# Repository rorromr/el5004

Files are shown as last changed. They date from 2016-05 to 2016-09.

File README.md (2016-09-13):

# EL5004: Teleoperación de Go Kart



Desarrollo de un sistema de actuación y teleoperación de un vehículo tipo Go Kart.

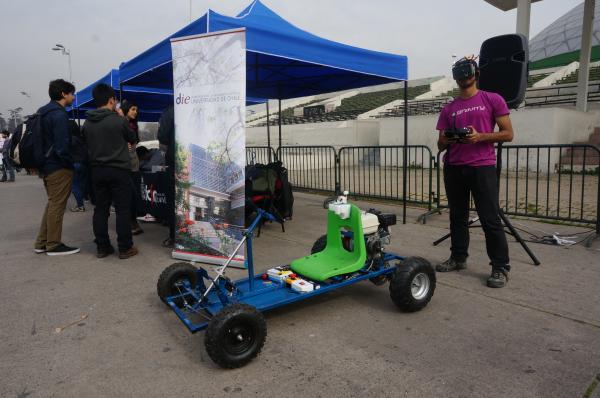
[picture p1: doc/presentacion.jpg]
 

Estructura:

```
el5004
|
+-- arduino [Software]
|
+-- doc [Documentación]
|
+-- cad [Archivos CAD]
|
+-- gokart_serial [Interfaz serial con PC]
|
+-- pcb [Diseño PCB]
|
+-- scripts [Scripts de compilación y CI]
```

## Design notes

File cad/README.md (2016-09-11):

# EL5004: Teleoperación de Go Kart

## CAD

Los archivos CAD fueron creados usando SolidWorks 2014 y estan disponibles [aquí](https://mega.nz/#!sts3RLpC!TGG8FULg5RGBNG4SyLwB-OSzpaIaMvL-rCDUFSoWiwc).

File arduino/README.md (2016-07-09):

# EL5004: Teleoperación de Go Kart

## Código para Arduino

La plataforma de desarrollo corresponde a Arduino Mega 2560.

El software se ha estructurado como una librería de Arduino. Para más información ver [librerías de Arduino]( https://www.arduino.cc/en/Guide/Libraries).

El directorio para la instalación de librerías de Arduino suele ser:
* Linux: `~/Arduino/libraries`
* OS X: `Documents/Arduino/libraries`
* Windows: `My Documents\Arduino\libraries`

## Librerías

### Dynamixel

Esta librería emplea la conexión serial 1 de Arduino Mega (TX1, RX1). El pin usado para cambiar la dirección de comunicación es configurado en el método `begin` de la librería. 

#### Instalación

Copiar el directorio `DynamixelSerial1` en `~/Arduino/libraries`

### GoKart

Contiene el código para el control del vehiculo GoKart.

```
arduino
|
+-- GoKart [Librería principal]
|   |
|   +-- examples
|       |-- dynamixel_test [Test de motores Dynamixel]
|       |-- gokart_dynamixel [Test motores Dynamixel usando interfaz GoKart]
|       |-- gokart_integration [Desarrollo de software principal]
|       |-- gokart_lcd_test [Test de pantalla LCD]
|       |-- msg_test [Test de serialización de mensajes]
|       |-- rf_test [Test de comunicación RF]
|       |-- rf_test2 [Test de comunicación RF con salida serial más rápida]
|       |-- serial_test [Test de comunicación serial]
|
```
#### Instalación

Copiar el directorio `GoKart` en `~/Arduino/libraries`

#### Problemas conocidos

La librería para el control de motores Dynamixel solo funciona usando un baudrate de 1.000.000 baud/s.

## Datasheet EX106

[Documento PDF](http://www.hizook.com/files/users/3/EX-106_Robotis_Dynamixel_Servo_UserGuide.pdf)

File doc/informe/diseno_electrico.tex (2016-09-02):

\section{Diseño eléctrico}

En esta sección se muestran los distintos elementos del desarrollo en el plano eléctrico y electrónico.

\subsection{Diagrama eléctrico}

La Figura \ref{de_diagrama} muestra el diagrama eléctrico principal, este cuenta con los siguientes elementos:
\begin{itemize}
    \item \textbf{Batería}: La batería corresponde a un pack de 4 celdas de polímero de litio. Posee un voltaje nominal de \SI{14.8}{\volt} y una capacidad de \SI{3300}{\milli\ampere\hour}. Este tipo de baterías se caracterizan por su gran densidad energética y capacidad de descarga, por lo es óptima para la operación de motores, pues usualmente requieren peaks corriente del orden de \SI{5}{\ampere}.
    \item \textbf{Panel de control}: En su interior contiene el microcontrolador y receptor de radio.
    \item \textbf{Interruptor principal}: Es el encargado de conectar la batería con el resto de los circuitos.
    \item \textbf{Interruptor de emergencia}: Desconecta la energía del bus de actuadores Dynamixel, no interfiere con la alimentación del panel de control.
    \item \textbf{Bus Dynamixel}: Este bus esta constituido por cuatro conductores. Dos de ellos proporcionan alimentación a los dispositivos conectados ($V_{cc}$ y tierra). Los otros dos corresponden a la señal diferencial del bus RS485.
\end{itemize}

\begin{figure}[H]
\begin{center}
	
	\caption{Diagrama elétrico principal.}
	\label{de_diagrama}
\end{center}
\end{figure}

\subsection{Sistema de radio}

Para la comunicación con el GoKart a través de telecomandos se está utilizando un transmisor de radiofrecuencias llamado Fly-Sky modelo FS-T6, junto a un receptor de 6 canales a 2.4 GHz llamado Fly-Sky modelo FS-R6B (ver en Figura \ref{rf}).

\begin{figure}[H]
    \centering
    \begin{subfigure}[b]{0.3\textwidth}
        \centering
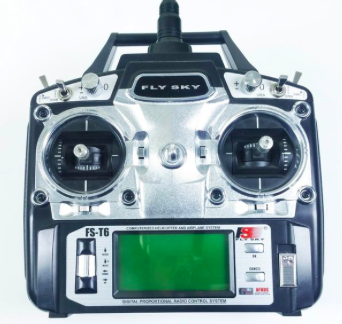
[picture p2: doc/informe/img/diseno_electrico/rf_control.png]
        
        \caption{Control remoto}
        \label{rf_control}
    \end{subfigure}
    \begin{subfigure}[b]{0.3\textwidth}
        \centering
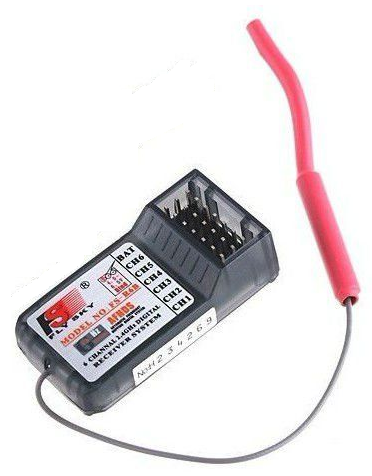
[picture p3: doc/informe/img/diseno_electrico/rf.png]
        
	    \caption{Receptor de radio}
	    \label{rf_img}
    \end{subfigure}
    \caption{Hardware utilizado para telecomandar el gokart}\label{rf}
\end{figure}

De la radio transmisora se utilizarán 3 comandos:
\begin{enumerate}
    \item {\textbf{Manilla izquierda:} movimientos UP y DOWN para acelerar y frenar, respectivamente.}
    \item {\textbf{Manilla derecha: } movimientos LEFT y RIGHT para dirección.}
    \item {\textbf{Switch superior izquierda:} para activar estado de emergencia. }
\end{enumerate}

De esta forma, el receptor utiliza 3 de sus 6 canales para recibir los datos, los que resultan ser números enteros con un rango entre 1000-1400, que corresponden al valor en \si{\micro\second} del up-time de la señal PWM recibida.

\subsection{Sistema embebido}

El sistema cuenta con un microcontrolador principal encargado de recibir los comandos desde el receptor de radio y enviar comandos de movimiento a los servomotores. El sistema usa como elemento principal una placa de desarrollo Arduino Mega 2560 \cite{arduino_mega}, que se muestra en la Figura \ref{arduino_mega_img}. La Tabla \ref{arduino_mega_tab} muestra las principales características de la placa de desarrollo.

\begin{table}[H]
\centering
\begin{tabular}{|l|l|}
\hline
Microcontrolador        & ATmega2560                              \\ \hline
Voltaje de operación    & \SI{5}{\volt}                           \\ \hline
Limites de alimentación & \SI{6}{\volt} a \SI{20}{\volt}          \\ \hline
GPIO                    & 54                                      \\ \hline
Entradas ADC            & 16                                      \\ \hline
Memoria Flash           & \SI{256}{\kilo\byte}                    \\ \hline
SRAM                    & \SI{8}{\kilo\byte}                      \\ \hline
Velocidad de reloj      & \SI{16}{\mega\hertz}                    \\ \hline
Puertos UART            & 4                                       \\ \hline
\end{tabular}
\caption{Características Arduino Mega 2560}
\label{arduino_mega_tab}
\end{table}

\begin{figure}[H]
\begin{center}
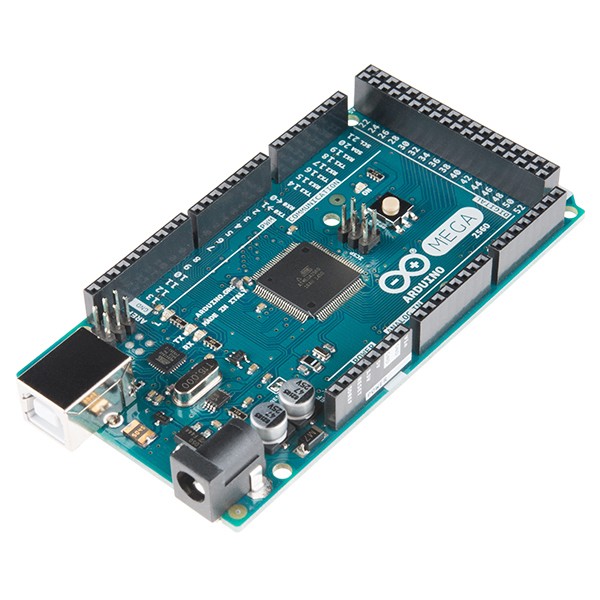
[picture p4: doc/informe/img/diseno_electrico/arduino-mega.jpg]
	
	\caption{Arduino Mega 2560.}
	\label{arduino_mega_img}
\end{center}
\end{figure}

\subsubsection{Pantalla LCD}

La pantalla LCD empleada corresponde a LCD \textit{keypad shield} \cite{arduino_lcd}, esta placa es compatible con el extendido controlador Hitachi HD44780. La Figura \ref{arduino_lcd} muestra la placa utilizada.

\begin{figure}[H]
\begin{center}
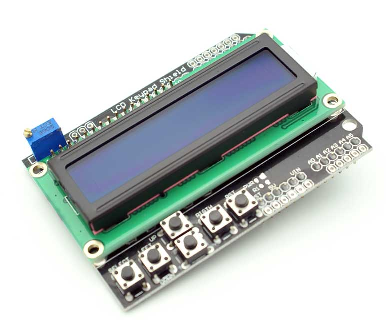
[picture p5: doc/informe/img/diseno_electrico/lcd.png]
	
	\caption{LCD \textit{keypad shield} utilizado.}
	\label{arduino_lcd}
\end{center}
\end{figure}

\subsubsection{Interfaz con motores Dynamixel}

Los actuadores utilizados en este proyecto corresponden al modelo Dynamixel EX-106+ fabricados por Robotis. Estos actuadores son ampliamente utilizados en aplicaciones robóticas, integran su propio controlador, encoder, driver e interfaz de comunicación que permite la conexión de múltiples actuadores usando como capa física un bus RS485.

Para la conversión del puerto UART del del microcontrolador al estándar RS485 es necesario un \textit{transceiver}, en está aplicación se uso un integrado SN75176BP de Texas Instruments \cite{ic_rs485}.

Para la comunicación con los actuadores Dynamixel es necesario usar un protocolo especificado por el fabricante \cite{motor_datasheet}, dado la gran extensión de estos motores existen librerías que proveen una interfaz de software que implementan el protocolo.

\subsubsection{PCB}

Para el montaje del receptor de radio y componentes necesarios para la comunicación con los motores Dynamixel, se diseñó y construyó una PCB que se se empotra de forma natural a la placa Arduino Mega, pues se ha usado el formato conocido como \textit{shield}.

La Figura \ref{de_pcb} muestra el diseño de la PCB, donde se ha considerado las conexiones para el \textit{transceiver} RS485, una pantalla LCD y potenciómetros para hacer una interfaz de usuario.

\begin{figure}[H]
\begin{center}
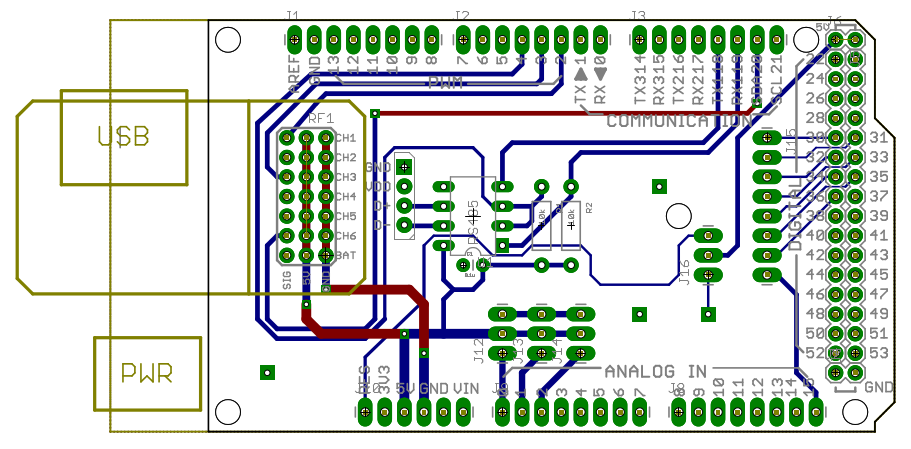
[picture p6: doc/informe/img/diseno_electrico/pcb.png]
	
	\caption{PCB con formato \textit{shield}.}
	\label{de_pcb}
\end{center}
\end{figure}

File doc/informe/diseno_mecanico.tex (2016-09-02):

\section{Diseño mecánico}

En esta sección se muestran los distintos elementos mecánicos desarrollados, se muestran los requerimientos, los mecanismos involucrados y la solución implementada de cada uno de los actuadores.

%%%%%% DIRECCION %%%%%%
\subsection{Dirección}

\subsubsection{Requerimientos}

Se requiere un sistema de actuación sobre el giro del goKart, el cual logre los \SI{60}{\degree} de movilidad que se tienen (30° tanto para izquierda como derecha, con respecto al centro). Además, debe cumplir los requerimientos de torque los cuales se midieron en condiciones estáticas con el fin de sobredimensionar lo requerido, obteniendo con ello un factor de seguridad. Los requerimientos se resumen en la Tabla \ref{sw} . El brazo para el torque corresponde a la distancia entre centro del volante y extremos (\SI{10}{\centi\meter}). 

\begin{table}[H]
\centering
\begin{tabular}{l|l|l|}
\cline{2-3}
                                & Torque \si{\newton\meter} & Ángulo giro \si{\degree} \\ \hline
\multicolumn{1}{|l|}{Derecha}   & 12,75                     & 30                       \\ \hline
\multicolumn{1}{|l|}{Izquierda} & 8,83                      & 30                       \\ \hline
\end{tabular}
\caption{Tabla de requerimientos para actuar dirección.}
\label{sw}
\end{table}

\subsubsection{Propuesta}

Se propone una sistema de engranes rectos acoplados tanto al eje de dirección como al motor utilizado. Este último corresponde a la serie Dynamixel EX-106+, que entrega un torque máximo de \SI{10.4}{\newton\meter} y un ángulo de giro de \SI{250}{\degree}, así que dado los requerimientos (\SI{60}{\degree}), se estable una relación de 3:1 en el sistema de engranes, con el fin de utilizar toda la resolución del encoder del motor. Por otro lado, esto permite no forzar al motor a su torque máximo, sino a un tercio de su capacidad, quedando sobredimensionado ante cualquier falla que ocurra (factor de seguridad de 2.5 entre torque máximo y torque exigido al motor).

Por recomendación, se nos sugirió usar engranes módulo 2, por lo que todos los cálculos para estos se basan en ese supuesto. En la Tabla \ref{engrane} se muestra un resumen de los parámetros de ambos engranes. La Figura \ref{eng} muestra un modelo de como quedaría el montaje. La plataforma que se construye para el motor considera el ángulo necesario para que ambos engranes queden alineados. Se diferencia entre una plancha fija (color gris) y una plancha roja (móvil). A este última va apernado el motor. El hecho de que sea móvil permite subir y bajar el engrane del motor para ajustar los dientes de este con los del otro engranaje. La fijación se realiza con pernos Parker de cabeza plana.

El engrane de dirección consta de un acople de \SI{65}{\milli\meter} de diámetro y 20 mm de ancho, el cual se usará para unirlo al eje de dirección mediante un pasador partido de 6 mm de diámetro. Además cuenta con una perforación central de 10 mm de diámetro que corresponde al diámetro del eje. 

%@TODO
%Para mayores detalles de medidas, revisar anexo.  

\begin{table}
\centering

\begin{tabular}{l|l|l|}
\cline{2-3}
                                          & Engrane motor & Engrane dirección \\ \hline
\multicolumn{1}{|l|}{Módulo}              & 2             & 2                 \\ \hline
\multicolumn{1}{|l|}{Diámetro exterior \si{\milli\meter}} & 46      &  136    \\ \hline
\multicolumn{1}{|l|}{Paso}                & 6.28          & 6.28              \\ \hline
\multicolumn{1}{|l|}{Número Dientes}      & 21            & 66                \\ \hline
\multicolumn{1}{|l|}{Altura cabeza de diente \si{\milli\meter}} & 4.32  & 4.32\\ \hline
\multicolumn{1}{|l|}{Ancho de engranes \si{\milli\meter}} & 10 & 10            \\ \hline
\end{tabular}
\caption{Parámetros de engranes}
\label{engrane}
\end{table}

\begin{figure}[H]
\begin{center}
    \begin{subfigure}{0.4\textwidth}
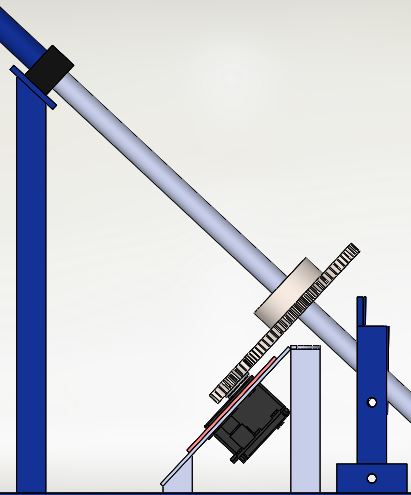
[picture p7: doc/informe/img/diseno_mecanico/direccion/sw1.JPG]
         
        \label{sw11}
    \end{subfigure}
    \begin{subfigure}{0.4\textwidth}
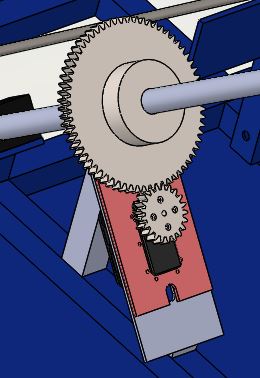
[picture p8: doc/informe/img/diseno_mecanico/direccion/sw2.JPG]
        
        \label{sw22}
    \end{subfigure}
    \caption{Diseño CAD del actuador de dirección}
    \label{eng}
\end{center}
\end{figure}

\subsubsection{Resultados}

La Figura \ref{engraneFinal} muestra el montaje final. En la plataforma del motor se incluyó una pieza rectangular que une a ambos pilares con el fin de utilizar pernos para el montaje en el chasis del auto. El engrane de dirección no tiene todo los dientes puesto que solo rota en \SI{60}{\degree}, por lo que se dentó un cuarto (\SI{90}{\degree}) del total. El acople de este mismo se disminuyo para reducir peso, quedando con \SI{15}{\milli\meter} de ancho. La posición de todo el montaje no quedó exactamente donde indica el CAD, dado que el escaso espacio dificultaba el montaje, por lo que se corrió hacia el otro extremo (el engrane de dirección se subió a lo largo del eje) y se ajustó el engrane del motor usando la plataforma móvil su máxima altura, con el fin de que los dientes de ambos engranen quedaran bien acoplados. Se tuvo que devastar los soporte plásticos negros que mantienen el eje de dirección (se ven en la figura \ref{eng}) para así acercar más la dirección (y el engrane) al motor.

Dado que el diseño del goKart contempla movilidad de su dirección a lo largo (el volante se puede hundir o acercar al usuario), se pueden desacoplar los engranes, en el caso que se quiera manejar de manera manual el auto. Esto conlleva el problema de que los dientes de ambos engranes no están fijos, pues la vibración propia del auto al estar encendido hace que la dirección vibre a su vez y los dientes se muevan un poco entre sí, sin desacoplarse. A futuro se propone fijar la dirección en una posición (volante fijo) tal que el sistema de engrane no se altere.

\begin{figure}[H]
\begin{center}
    \begin{subfigure}{0.4\textwidth}
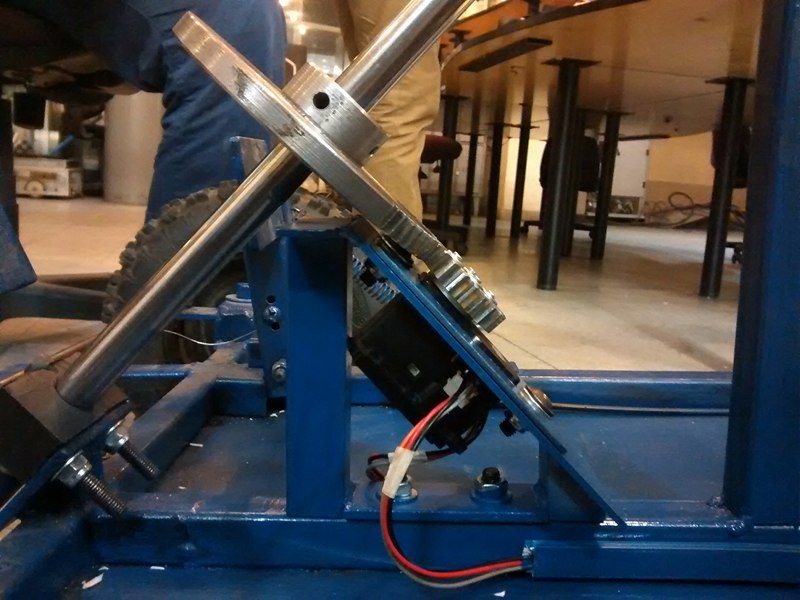
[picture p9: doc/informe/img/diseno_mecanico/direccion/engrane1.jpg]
         
        \label{sw1}
    \end{subfigure}
    \begin{subfigure}{0.4\textwidth}
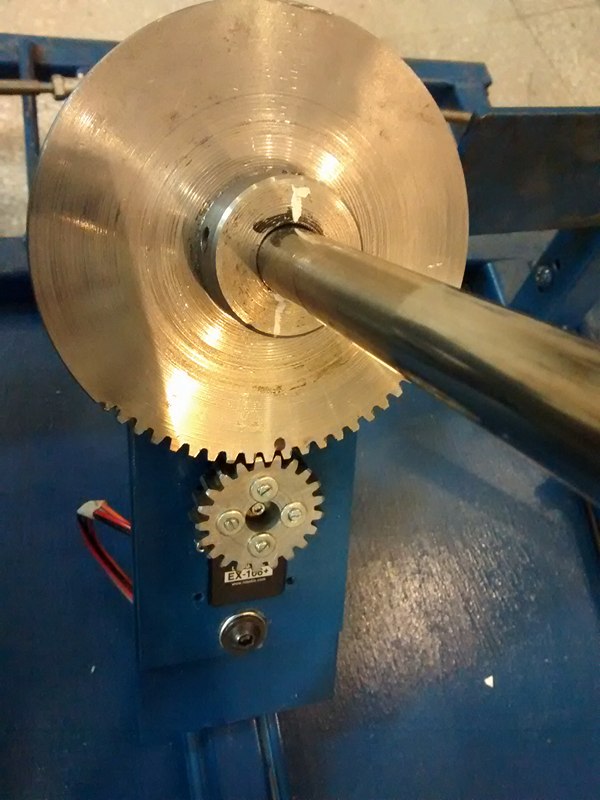
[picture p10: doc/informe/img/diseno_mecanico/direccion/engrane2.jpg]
        
        \label{sw2}
    \end{subfigure}
    \caption{Implementación del actuador de dirección}
    \label{engraneFinal}
\end{center}
\end{figure}

%%%%%% FRENO %%%%%%
\subsection{Freno}

\subsubsection{Requerimientos}
La implementación de este sistema tiene por objetivo actuar eléctricamente sobre el freno sin comprometer al sistema manual del vehículo, es decir un sistema de frenado mixto. Esto implica que si se acciona el frenado eléctricamente, el piloto tenga la posibilidad de usar el freno manual en todo momento, y viceversa.

El sistema manual consiste en un freno hidráulico accionado por un pistón conectado a una vara móvil con la que se comprime el líquido en su interior (Figura \ref{piston}).

\begin{figure}[H]
\begin{center}
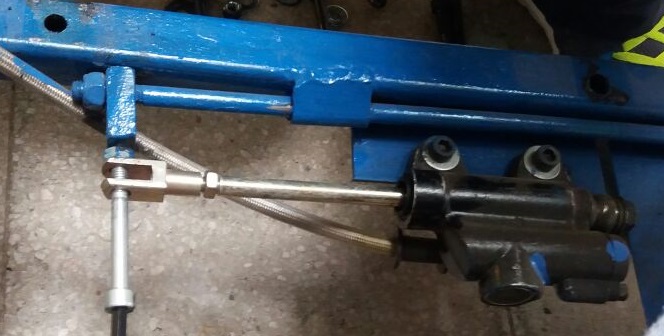
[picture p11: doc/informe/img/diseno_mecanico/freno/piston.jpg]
	
	\caption{Pistón del sistema de freno del vehículo.}
	\label{piston}
\end{center}
\end{figure}

\subsubsection{Propuesta}

La solución propuesta consiste en añadir una pieza móvil (Figura \ref{cad_roldana}, pieza naranja) denominada roldana, que accione el freno hidráulico del sistema original mediante un adaptador que otorgue el desacoplamiento de ambos sistemas (Figura \ref{cad_roldana}, pieza gris). Cabe destacar que el adaptador sustituye a la pieza que empuja al pistón de la Figura \ref{piston}. El movimiento mecánico lo accionará un servomotor Dynamixel EX-106+ \cite{motor_datasheet}.

\begin{figure}[H]
\begin{center}
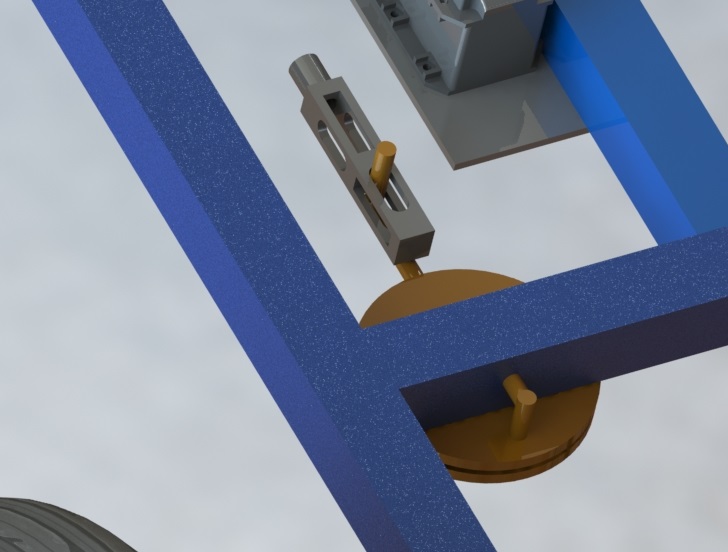
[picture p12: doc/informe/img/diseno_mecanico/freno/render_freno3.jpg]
	
	\caption{CAD roldana y adaptador del freno.}
	\label{cad_roldana}
\end{center}
\end{figure}

El objetivo es que la roldana empuje el adaptador al accionar el servomotor. Para ello se propone que uno de los extremos de la guía de la roldana esté fijo, mientras el otro se conecte al disco de giro del servomotor. De esta forma, al accionar el motor, variará la longitud efectiva de la guía y con ello la posición de la roldana. En particular se midió que la retracción necesaria que se le debe aplicar al pistón para un frenado completo es de 15 mm, por lo que la guía debería reducir su longitud efectiva en 30 mm (asumiendo simetría de la guía con respecto al eje de movimiento de la roldana).

Con el fin de generar el menor roce posible para el movimiento de la roldana se determinó que la guía de ésta estuviera paralela al eje de movimiento, restringiendo las posibles ubicaciones del servomotor. En la Figura \ref{cad_freno} se muestra la posición del servomotor y del chasis añadido que lo sostiene. También se observan las tres piezas sostenedoras de la roldana: una superior atravesando horizontalmente el chasis, y dos pernos inferiores por los que se mueve la roldana.

\begin{figure}[H]
\begin{center}
    \begin{subfigure}{0.4\textwidth}
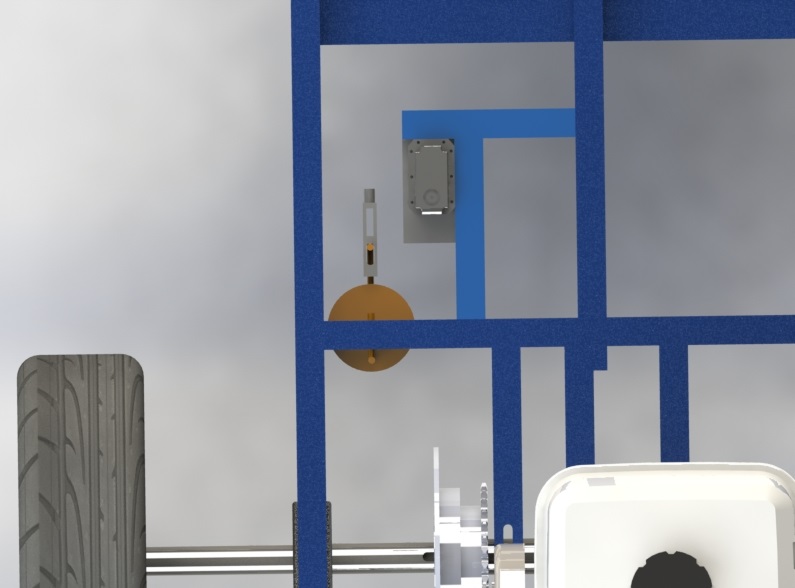
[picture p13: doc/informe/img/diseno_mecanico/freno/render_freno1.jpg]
         
        \label{freno1}
    \end{subfigure}
    \begin{subfigure}{0.4\textwidth}
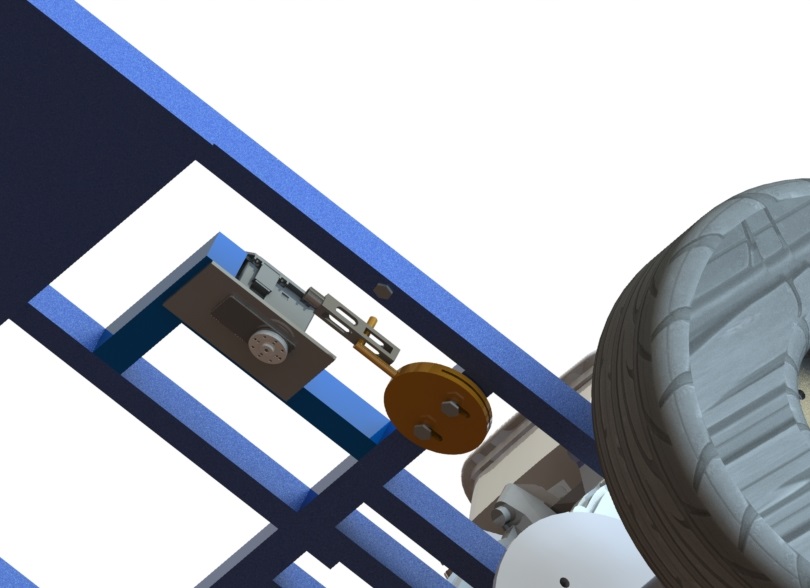
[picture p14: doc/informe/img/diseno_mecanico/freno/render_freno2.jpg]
        
        \label{freno2}
    \end{subfigure}
    \caption{Diseño CAD del actuador del freno.}
    \label{cad_freno}
\end{center}
\end{figure}

\subsubsection{Resultados}

Las piezas principales del sistema (roldana y adaptador) resultaron de la forma esperada. No obstante, se realizaron ligeros cambios con respecto al montaje de la roldana, pues solamente se implementaron dos de las tres piezas sostenedoras (los pernos) debido al limitado espacio disponible entre la roldana y el disco de freno (Figura \ref{res_freno}).

En la Figura \ref{res_freno} se muestran tres estados distintos del sistema de frenado mixto. La Figura \ref{res_freno1} muestra el estado de reposo, es decir que el vehículo no está frenado. En la Figura \ref{res_freno2} se observa el desplazamiento de la roldana debido al accionamiento del servomotor, causando el frenado del goKart sin necesidad de actuar en el freno manual. La Figura \ref{res_freno3} indica un frenado manual sin movimiento del servomotor por lo que la roldana permanece en la posición de reposo y la guía se destensa levemente, pero no lo suficiente como para desprenderse de la roldana. En el caso de un frenado simultáneo (manual y eléctrico) se produce un resultado similar al frenado manual, con la diferencia de que la roldana se desplaza y la guía permanece tensa.

\begin{figure}[H]
\begin{center}
    \begin{subfigure}{0.3\textwidth}
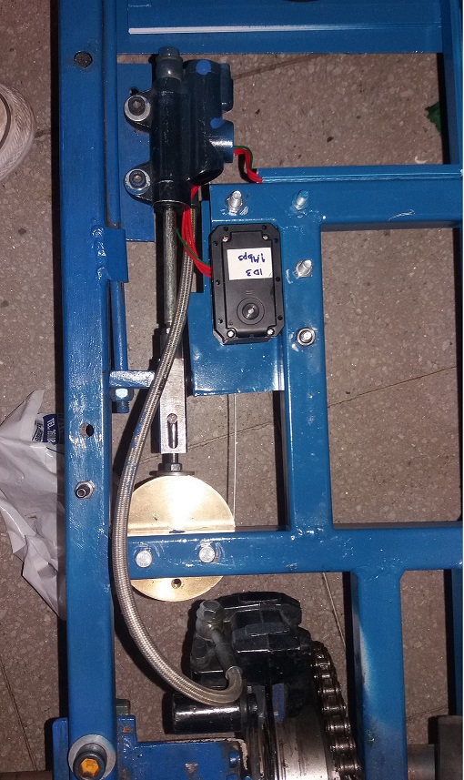
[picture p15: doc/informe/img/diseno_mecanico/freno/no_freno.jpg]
         
        \caption{Sistema en reposo.}
        \label{res_freno1}
    \end{subfigure}
    \begin{subfigure}{0.3\textwidth}
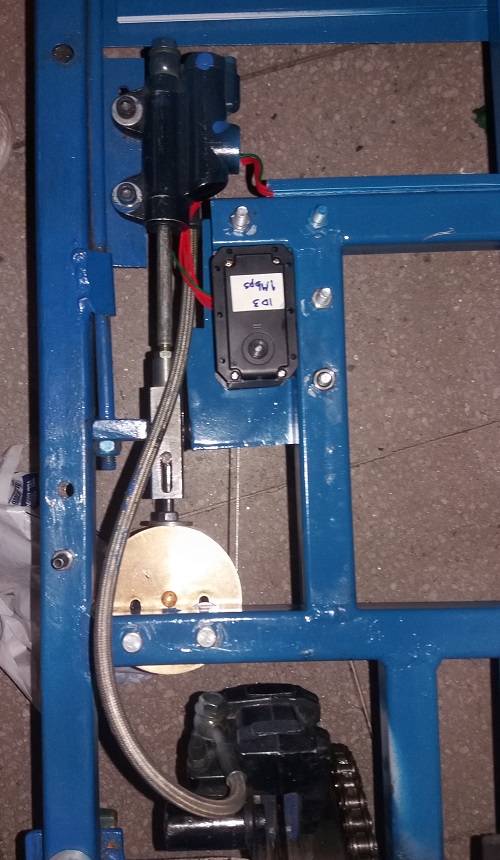
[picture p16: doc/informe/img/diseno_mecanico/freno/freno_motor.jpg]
        
        \caption{Freno accionado por motor.}
        \label{res_freno2}
    \end{subfigure}
    \begin{subfigure}{0.3\textwidth}
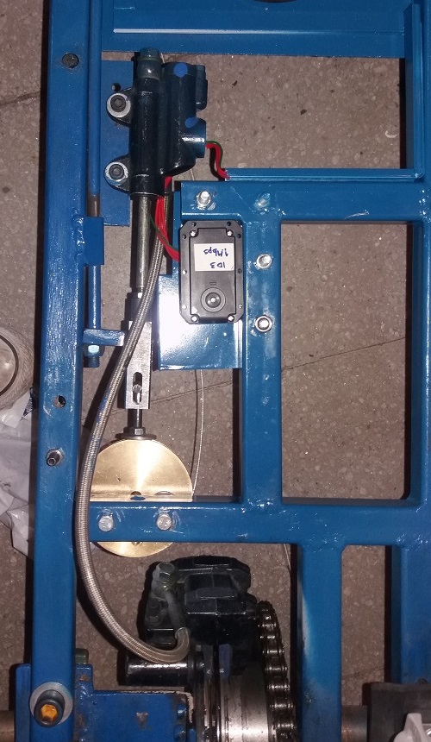
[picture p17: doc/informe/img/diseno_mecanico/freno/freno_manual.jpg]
        
        \caption{Freno accionado manualmente.}
        \label{res_freno3}
    \end{subfigure}
    \caption{Actuador del freno en sus estados principales.}
    \label{res_freno}
\end{center}
\end{figure}

%%%%%% ACELERADOR %%%%%%
\subsection{Acelerador}

\subsubsection{Requerimientos}

De la misma forma que el frenado, la implementación de este sistema tiene por objetivo actuar eléctricamente sobre el acelerador sin comprometer al sistema manual del vehículo, es decir un sistema de aceleración mixto. Esto implica que el acelerador se pueda accionar tanto eléctrico como manualmente. 
El sistema manual consiste en una piola conectada directamente al pedal de aceleración; y en su otro extremo, al acelerador del motor del goKart.

\subsubsection{Propuesta}
Se propone incluir una pieza intermediaria entre los actuadores y la piola conectada al acelerador del motor. La pieza corresponde a una platina de acero móvil a través de unos ejes (Figura \ref{platina}), en donde por un extremo se conecta la piola del acelerador, y por el otro se encajan las piolas de los sistemas manual y eléctrico. El actuador eléctrico corresponde a un servomotor Dynamixel ex-106+ \cite{motor_datasheet}.

\begin{figure}[H]
\begin{center}
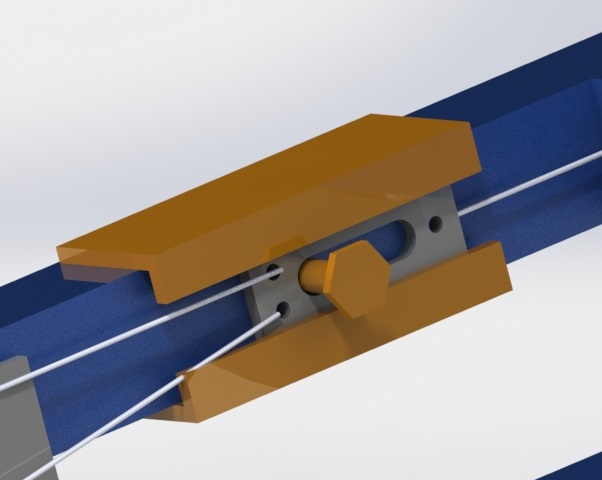
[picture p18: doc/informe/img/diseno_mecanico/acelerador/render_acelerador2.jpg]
	
	\caption{CAD de platina con los ejes como guía.}
	\label{platina}
\end{center}
\end{figure}

Las tres secciones de piola conectadas a la platina deben estar tensadas en el reposo, lo que causa el movimiento de la platina si se presiona el pedal del acelerador (sistema manual) o si se rota el disco de giro servomotor (sistema eléctrico) y por ende, se accionará el acelerador del motor del goKart (Figura \ref{cad_acelerador}). Esta propuesta parte de la premisa que las piolas pueden aflojarse cierta cantidad, pues al momento de activar un sistema de acelerador, la piola del otro quedará en desuso. Cabe destacar que el desplazamiento máximo de la piola para acelerar, en el sistema manual original, es de aproximadamente 3 cm.

\begin{figure}[H]
\begin{center}
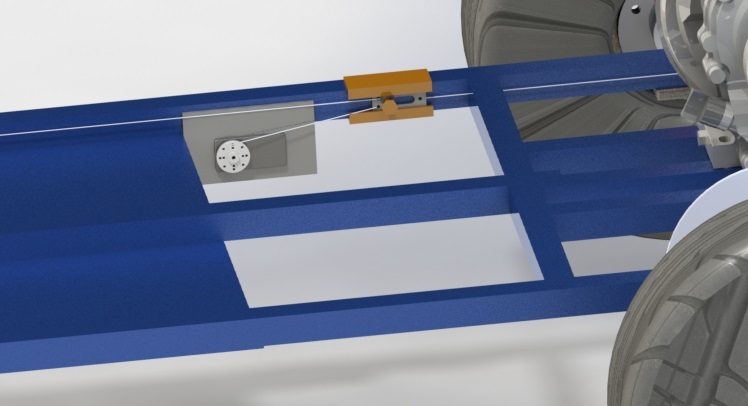
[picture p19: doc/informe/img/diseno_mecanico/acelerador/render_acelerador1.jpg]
	
	\caption{Diseño CAD del actuador del acelerador.}
	\label{cad_acelerador}
\end{center}
\end{figure}

Como medida de seguridad se optó por ubicar un resorte en el extremo de la platina cercano al motor, de manera que el sistema tienda a detener la aceleración con la fuerza del resorte y no del sistema intrínseco del motor del goKart.

\subsubsection{Resultados}

La idea de deslizar una pieza por una guía se mantuvo, con la diferencia del tipo de piezas a utilizar. Finalmente se implementó un sistema con una corredera telescópica con rodamientos. Esto fue por el ínfimo roce que se opone al movimiento en comparación a una platina de acero.

Por otro lado, para generar holguras en las piolas y evitar fuerzas no deseadas por la piola en desuso cuando se active uno de los dos sistemas de aceleración, se optó por conectar las piolas a la corredera por medio de topes móviles (Figura \ref{res_acelerador}). La configuración en reposo consiste en tener las tres piolas tensas, y al momento de accionar un actuador la piola correspondiente jalará la corredera, mientras la otra estará en reposo, desacoplándose a la corredera.

En la Figura \ref{res_acelerador1} se muestra el estado en reposo, en donde las tres piolas se encuentran en una tensión que ocasiona que la corredera esté cercana al motor del goKart. La Figura \ref{res_acelerador2} indica una aceleración efectuada por el servomotor, de manera que la corredera se aleja del motor del goKart y la piola de sistema manual queda en un reposo parcial. Por último, en la Figura \ref{res_acelerador3} se tiene una aceleración manual, por lo que se obseva la corredera alejada del motor del vehículo, mientras que la piola del servomotor está en desuso.

\begin{figure}[H]
\begin{center}
    \begin{subfigure}{0.45\textwidth}
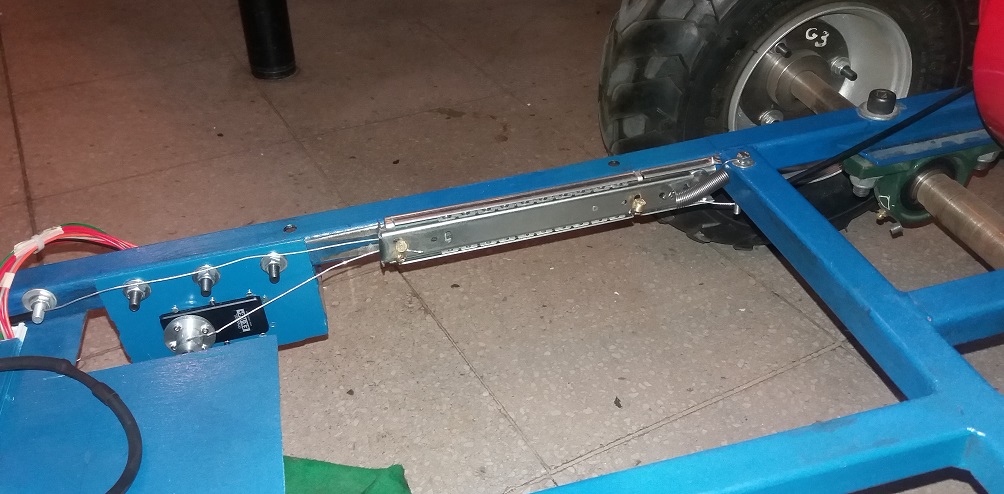
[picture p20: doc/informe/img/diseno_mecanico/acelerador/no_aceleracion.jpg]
         
        \caption{Sistema en reposo.}
        \label{res_acelerador1}
    \end{subfigure}
    \begin{subfigure}{0.45\textwidth}
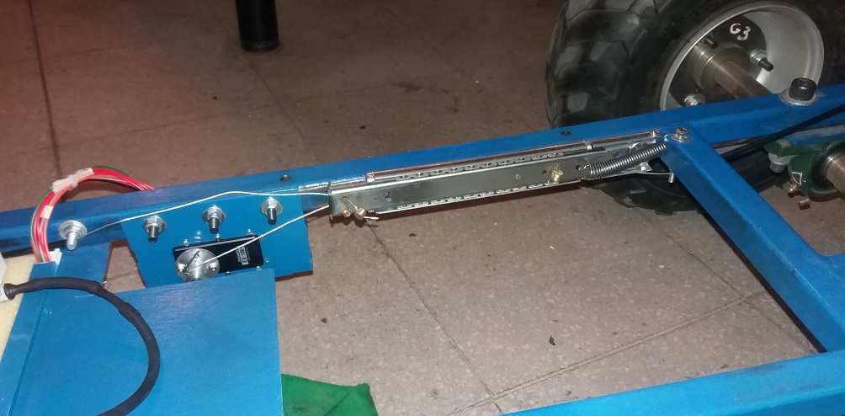
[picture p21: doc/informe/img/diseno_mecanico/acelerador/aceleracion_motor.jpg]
        
        \caption{Sistema accionado por motor.}
        \label{res_acelerador2}
    \end{subfigure}
    
    \begin{subfigure}{0.45\textwidth}
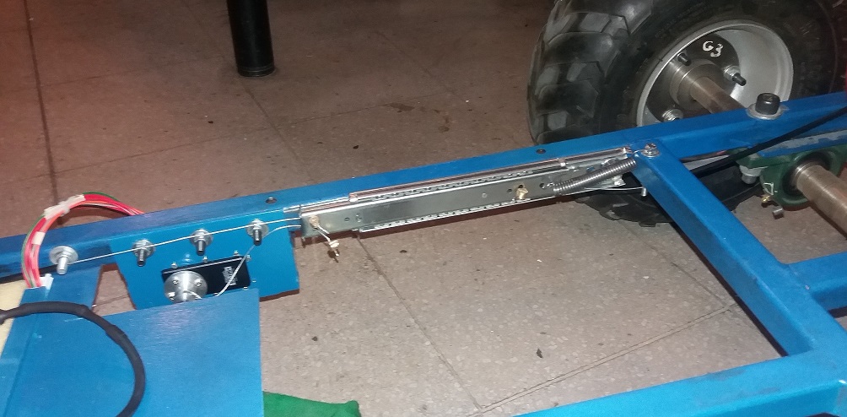
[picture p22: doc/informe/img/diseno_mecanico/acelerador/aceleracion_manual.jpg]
        
        \caption{Sistema accionado manualmente.}
        \label{res_acelerador3}
    \end{subfigure}
    
    \caption{Actuador del acelerador en sus estados principales.}
    \label{res_acelerador}
\end{center}
\end{figure}

Por otro lado, en las imágenes de la Figura \ref{res_acelerador} se puede observar un resorte en el extremo de la corredera cercano al motor del goKart. Es el resorte de seguridad que se encarga de devolver la corredera al estado de reposo mientras ninguno de los sistemas de aceleración se activen.

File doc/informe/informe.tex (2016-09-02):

\documentclass[11pt,letterpaper,notitlepage]{article}

% Codificacion Windows
%\usepackage[latin1]{inputenc}
%\usepackage[spanish]{babel}

% Codificación GNU/Linux
\usepackage[utf8]{inputenc}
\usepackage[activeacute,spanish,es-tabla]{babel}

% Margenes
\usepackage{anysize}
\marginsize{2cm}{2cm}{2cm}{2cm}

% Estilo de pagina
\usepackage{fancyhdr}
\pagestyle{fancy}
\fancyhead[l]{\small EL5004 - Taller de Diseño}
\fancyhead[r]{}

% Simbolos y letras para matemáticas
\usepackage{amssymb,amsmath,amsfonts}

% Colores
\usepackage{color}
\definecolor{rojo}{RGB}{255,26,34}
\definecolor{gris}{RGB}{104,108,113}
\definecolor{mygreen}{RGB}{28,172,0} % color values Red, Green, Blue
\definecolor{mylilas}{RGB}{170,55,241}

% Elementos Flotantes (Figuras y Tablas)

\usepackage{graphicx}
\graphicspath{ {img/} }
\usepackage{caption}
\usepackage{subcaption}
\usepackage{float}
\usepackage[binary-units=true]{siunitx}
\usepackage{multicol}
\usepackage{multirow}
\usepackage{epstopdf}
\usepackage{enumerate}
\usepackage{wrapfig}
\usepackage{enumitem}
\usepackage{hyperref}
\usepackage[numbered,framed]{mcode} %Código MATLAB
\hypersetup{
    colorlinks,
    linkcolor={gris},
    citecolor={gris},
    urlcolor={gris}
}
%Codigo fuente

\usepackage{listings}
\setlength{\headheight}{30pt} 

% Linea
\newcommand{\HRule}{\rule{\linewidth}{.4mm}}
\renewcommand{\lstlistingname}{Código fuente}
\renewcommand{\lstlistlistingname}{Indice de códigos fuente}

\input{portada}

\begin{document}

\portada{Diseño de actuación y teleoperación de vehículo tipo Gokart}{Informe de Avance}

\newpage
\thispagestyle{empty}
\tableofcontents
\newpage

\vspace*{-0.8cm}

\input{introduccion.tex}

\input{diseno_mecanico.tex}

\input{diseno_electrico.tex}

\input{software.tex}

\nocite{*}
\bibliographystyle{plain}
\bibliography{bibliografia}

\end{document}

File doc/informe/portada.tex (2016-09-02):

\newcommand{\portada}[3]{

\begin{titlepage}

%Encabezado
\begin{wrapfigure}{l}{.6cm}
\vspace{-0.65cm}

\end{wrapfigure}
\hspace*{0.3cm}
\textsc{\color{rojo}\hspace{2.2cm}Departamento de Ingeniería Eléctrica}\\
\hspace*{0.3cm}
\textsc{\color{gris}\hspace{2.8cm}Facultad de Ciencias Físicas y Matemáticas}\\
\hspace*{0.3cm}
\textsc{\color{gris}\hspace{2.8cm}Universidad de Chile}\\
\hspace*{0.3cm}
\textsc{\color{gris}\hspace{2.8cm}EL5004 - Taller de Diseño}\\

% Titulo
\begin{center}
~\\[4.5cm]
{\color{gris} \Large \textbf{#2}}
\HRule~ \\[0.8cm]
{ \Huge \textup \bfseries  #1}\\[0.4cm]
\HRule ~\\[1.5cm]
\end{center}
\begin{minipage}{.5\textwidth}
~
\end{minipage}
%Datos
\begin{minipage}{.5\textwidth}
\begin{flushright}
\begin{tabular}{l}
\emph{Profesor:} \\
{\small Marcos Orchard}\\[0.3cm]
\emph{Profesores Auxiliares:} \\
{\small Alejandro Toledo}\\
{\small Isao Parra}\\[0.3cm]
\emph{Estudiantes:}\\
{\small Matías Godoy}\\
{\small David Gómez}\\
{\small Eduardo Hormazábal}\\
{\small Rodrigo Muñoz}\\
{\small Sebastián Piña}\\
{\small Matías Silva}\\
{\small Yoshiro Tsutsumi}\\[.3cm]
\emph{Fecha:}\\
{\small \today}
\end{tabular}
\end{flushright}
\end{minipage}

\end{titlepage}
}

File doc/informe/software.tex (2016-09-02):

\section{Software}
El software que ejecuta el microcontrolador para comunicar la radio transmisora y los actuadores en el auto se realizó utilizando un modelo de comunicación robusto, que garantizara el correcto funcionamiento del auto, activara rápidamente los casos de emergencia y ofreciera fácilmente una forma de comunicar la información al usuario del auto a través de una pantalla LCD (ver Sección 3.3).

Dado que el el \textit{toolchain} AVR GCC, usado para compilar el código para el microcontrolador, soporta el lenguaje C++, se hace en uso extensivo de programación orientada a objetos. Los elementos principales dentro del software (clases dentro del código) se detallan a continuación:
\begin{itemize}
    \item{\textbf{GoKartHW:}} Es el objeto principal o cerebro del código, al inicializarlo se inician los objetos que caracterizan los actuadores, la comunicación con el transmisor y con el LCD. También maneja el estado de emergencia, que implica detener frenar el auto y dejarlo con dirección hacia el centro.
    \item{\textbf{Dxl servo:}} Es el objeto encargado de la comunicación con los motores Dynamixel y configura los parámetros de velocidad, torque y posiciones mínimas y máximas que tienen actuadores. Estos objetos heredan de esta clase: 
    \begin{enumerate}
        \item{\textbf{Throttle:} Es el objeto que representa al actuador del acelerador y configura sus parámetros acorde a las características físicas de ese actuador en el montaje.}
        \item{\textbf{Brake:} Es el objeto que representa al actuador del freno y configura sus parámetros acorde a las características físicas de ese actuador en el montaje.}
        \item{\textbf{Steering Wheel:} Es el objeto que representa al actuador ligado al manubrio y configura sus parámetros acorde a las características físicas de ese actuador en el montaje.}
    \end{enumerate}
    
    \item{\textbf{RFInterface:} Es el objeto que controla el proceso de lectura de datos del receptor desde el transmisor RF. Este objeto recibe estos datos, los valida (según una configuración propia) y mapea hacia los actuadores. En caso de que los datos estén corruptos o no se estén recibiendo, entonces comanda al Gokart al estado de emergencia.}
    \item{\textbf{LCD:} Es el objeto que controla la pantalla LCD, su escritura y la forma en que se muestren y limpien los datos en la pantalla. Por tanto, a través de este objeto el Gokart envía los mensajes de los procesos que desee mostrar.}
\end{itemize}

Se ha hecho uso de herramientas de control de versiones e integración continua para el desarrollo de software de forma colaborativa. Esto permite que, de forma automatizada, cada aporte sea validado antes de su integración en el desarrollo principal.

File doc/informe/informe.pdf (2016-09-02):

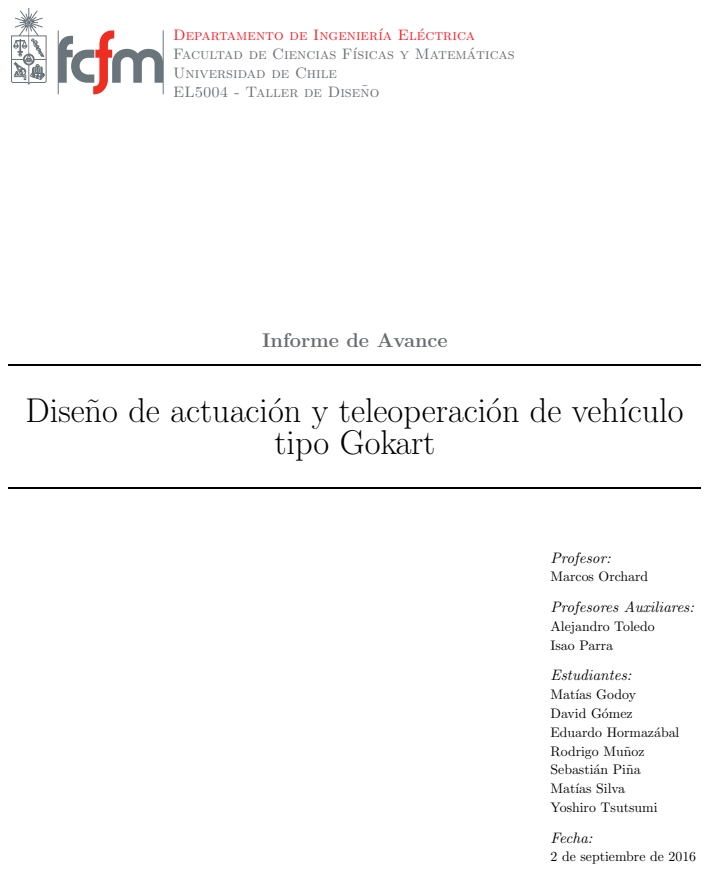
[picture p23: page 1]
tipo Gokart; Profesor:; Marcos Orchard; Profesores Auxiliares:; Alejandro Toledo; Isao Parra

Departamento de Ingeniería Electrica ´

Facultad de Ciencias Físicas y Matematicas ´

Universidad de Chile

EL5004 - Taller de Disenõ

Informe de Avance

Diseño de actuación y teleoperación de vehículo

Estudiantes:
Matías Godoy
David Gómez
Eduardo Hormazábal
Rodrigo Muñoz
Sebastián Piña
Matías Silva
Yoshiro Tsutsumi

Fecha:
2 de septiembre de 2016

## Índice

1. Introducción | 2
2. Diseño mecánico | 2
3. Diseño eléctrico | 9
4. Software | 13

EL5004 - Taller de Diseño

## 1. Introducción

Este trabajo se enmarca dentro del contexto del curso EL5004 Taller de Diseño, en el que se lleva a cabo un proyecto multidisciplinario entre estudiantes de ingeniería mecánica e ingeniería eléctrica, con el fin de lograr el acercamiento entre ambas disciplinas y el aprendizaje que esto conlleva, no solo de trabajo en equipo sino de acercar a los estudiantes a lo que corresponde a un proyecto real junto a todas sus partes: concebir, diseñar, implementar y operar. En este caso, se propone desarrollar una teleoperación de un vehículo tipo goKart construido por alumnos del departamento de ingeniería mecánica. Esto es, comandar a distancia las acciones de giro, aceleración y freno de este vehículo. Para ello se debe realizar un diseño mecánico para el montaje de los nuevos mecanismos, como así un diseño eléctrico de la conexión y comunicación entre los actuadores.

## 2. Diseño mecánico

En esta sección se muestran los distintos elementos mecánicos desarrollados, se muestran los requerimientos, los mecanismos involucrados y la solución implementada de cada uno de los actuadores.

### 2.1. Dirección

### 2.1.1. Requerimientos

Se requiere un sistema de actuación sobre el giro del goKart, el cual logre los 60° de movilidad que se tienen (30° tanto para izquierda como derecha, con respecto al centro). Además, debe cumplir los requerimientos de torque los cuales se midieron en condiciones estáticas con el fin de sobredimensionar lo requerido, obteniendo con ello un factor de seguridad. Los requerimientos se resumen en la Tabla 1 . El brazo para el torque corresponde a la distancia entre centro del volante y extremos (10 cm).

Torque N m | Angulo giro ´ °
Derecha | 12,75 | 30
Izquierda | 8,83 | 30

Tabla 1: Tabla de requerimientos para actuar dirección.

### 2.1.2. Propuesta

Se propone una sistema de engranes rectos acoplados tanto al eje de dirección como al motor utilizado. Este último corresponde a la serie Dynamixel EX-106+, que entrega un torque máximo de 10.4 N m y un ángulo de giro de 250°, así que dado los requerimientos (60°), se estable una relación de 3:1 en el sistema de engranes, con el fin de utilizar toda la resolución del encoder del motor. Por otro lado, esto permite no forzar al motor a su torque máximo, sino a un tercio de su capacidad, quedando sobredimensionado ante cualquier falla que ocurra (factor de seguridad de 2.5 entre torque máximo y torque exigido al motor). Por recomendación, se nos sugirió usar engranes módulo 2, por lo que todos los cálculos para estos se basan en ese supuesto. En la Tabla 2 se muestra un resumen de los parámetros de ambos engranes. La Figura 1 muestra un modelo de como quedaría el montaje. La plataforma que se construye para el motor considera el ángulo necesario para que ambos engranes queden alineados. Se diferencia entre una plancha

EL5004 - Taller de Diseño

Engrane motor | Engrane dirección
Módulo | 2 | 2
Diámetro exterior mm | 46 | 136
Paso | 6.28 | 6.28
Número Dientes | 21 | 66
Altura cabeza de diente mm | 4.32 | 4.32
Ancho de engranes mm | 10 | 10

Tabla 2: Parámetros de engranes

fija (color gris) y una plancha roja (móvil). A este última va apernado el motor. El hecho de que sea móvil permite subir y bajar el engrane del motor para ajustar los dientes de este con los del otro engranaje. La fijación se realiza con pernos Parker de cabeza plana.
El engrane de dirección consta de un acople de 65 mm de diámetro y 20 mm de ancho, el cual se usará para unirlo al eje de dirección mediante un pasador partido de 6 mm de diámetro. Además cuenta con una perforación central de 10 mm de diámetro que corresponde al diámetro del eje.

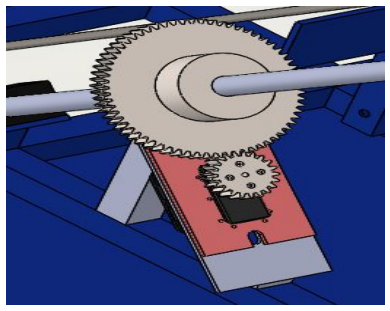
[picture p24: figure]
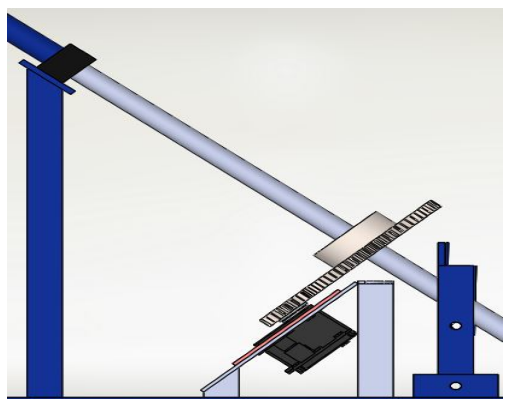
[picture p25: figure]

Figura 1: Diseño CAD del actuador de dirección

### 2.1.3. Resultados

La Figura 2 muestra el montaje final. En la plataforma del motor se incluyó una pieza rectangular que une a ambos pilares con el fin de utilizar pernos para el montaje en el chasis del auto. El engrane de dirección no tiene todo los dientes puesto que solo rota en 60°, por lo que se dentó un cuarto (90°) del total. El acople de este mismo se disminuyo para reducir peso, quedando con 15 mm de ancho. La posición de todo el montaje no quedó exactamente donde indica el CAD, dado que el escaso espacio dificultaba el montaje, por lo que se corrió hacia el otro extremo (el engrane de dirección se subió a lo largo del eje) y se ajustó el engrane del motor usando la plataforma móvil su máxima altura, con el fin de que los dientes de ambos engranen quedaran bien acoplados. Se tuvo que devastar los soporte plásticos negros que mantienen el eje de dirección (se ven en la figura 1) para así acercar más la dirección (y el engrane) al motor.
Dado que el diseño del goKart contempla movilidad de su dirección a lo largo (el volante se puede hundir o acercar al usuario), se pueden desacoplar los engranes, en el caso que se quiera manejar de

EL5004 - Taller de Diseño

manera manual el auto. Esto conlleva el problema de que los dientes de ambos engranes no están fijos, pues la vibración propia del auto al estar encendido hace que la dirección vibre a su vez y los dientes se muevan un poco entre sí, sin desacoplarse. A futuro se propone fijar la dirección en una posición (volante fijo) tal que el sistema de engrane no se altere.


Figura 2: Implementación del actuador de dirección

### 2.2. Freno

### 2.2.1. Requerimientos

La implementación de este sistema tiene por objetivo actuar eléctricamente sobre el freno sin comprometer al sistema manual del vehículo, es decir un sistema de frenado mixto. Esto implica que si se acciona el frenado eléctricamente, el piloto tenga la posibilidad de usar el freno manual en todo momento, y viceversa.
El sistema manual consiste en un freno hidráulico accionado por un pistón conectado a una vara móvil con la que se comprime el líquido en su interior (Figura 3).


Figura 3: Pistón del sistema de freno del vehículo.

EL5004 - Taller de Diseño

### 2.2.2. Propuesta

La solución propuesta consiste en añadir una pieza móvil (Figura 4, pieza naranja) denominada roldana, que accione el freno hidráulico del sistema original mediante un adaptador que otorgue el desacoplamiento de ambos sistemas (Figura 4, pieza gris). Cabe destacar que el adaptador sustituye a la pieza que empuja al pistón de la Figura 3. El movimiento mecánico lo accionará un servomotor Dynamixel EX-106+ [4].


Figura 4: CAD roldana y adaptador del freno.

El objetivo es que la roldana empuje el adaptador al accionar el servomotor. Para ello se propone que uno de los extremos de la guía de la roldana esté fijo, mientras el otro se conecte al disco de giro del servomotor. De esta forma, al accionar el motor, variará la longitud efectiva de la guía y con ello la posición de la roldana. En particular se midió que la retracción necesaria que se le debe aplicar al pistón para un frenado completo es de 15 mm, por lo que la guía debería reducir su longitud efectiva en 30 mm (asumiendo simetría de la guía con respecto al eje de movimiento de la roldana).
Con el fin de generar el menor roce posible para el movimiento de la roldana se determinó que la guía de ésta estuviera paralela al eje de movimiento, restringiendo las posibles ubicaciones del servomotor. En la Figura 5 se muestra la posición del servomotor y del chasis añadido que lo sostiene. También se observan las tres piezas sostenedoras de la roldana: una superior atravesando horizontalmente el chasis, y dos pernos inferiores por los que se mueve la roldana.

EL5004 - Taller de Diseño


Figura 5: Diseño CAD del actuador del freno.

### 2.2.3. Resultados

Las piezas principales del sistema (roldana y adaptador) resultaron de la forma esperada. No obstante, se realizaron ligeros cambios con respecto al montaje de la roldana, pues solamente se implementaron dos de las tres piezas sostenedoras (los pernos) debido al limitado espacio disponible entre la roldana y el disco de freno (Figura 6).
En la Figura 6 se muestran tres estados distintos del sistema de frenado mixto. La Figura 6a muestra el estado de reposo, es decir que el vehículo no está frenado. En la Figura 6b se observa el desplazamiento de la roldana debido al accionamiento del servomotor, causando el frenado del goKart sin necesidad de actuar en el freno manual. La Figura 6c indica un frenado manual sin movimiento del servomotor por lo que la roldana permanece en la posición de reposo y la guía se destensa levemente, pero no lo suficiente como para desprenderse de la roldana. En el caso de un frenado simultáneo (manual y eléctrico) se produce un resultado similar al frenado manual, con la diferencia de que la roldana se desplaza y la guía permanece tensa.

EL5004 - Taller de Diseño


(a) Sistema en reposo. | (b) Freno accionado por motor. (c) Freno accionado manualmente.

Figura 6: Actuador del freno en sus estados principales.

### 2.3. Acelerador

### 2.3.1. Requerimientos

De la misma forma que el frenado, la implementación de este sistema tiene por objetivo actuar eléctricamente sobre el acelerador sin comprometer al sistema manual del vehículo, es decir un sistema de aceleración mixto. Esto implica que el acelerador se pueda accionar tanto eléctrico como manualmente. El sistema manual consiste en una piola conectada directamente al pedal de aceleración; y en su otro extremo, al acelerador del motor del goKart.

### 2.3.2. Propuesta

Se propone incluir una pieza intermediaria entre los actuadores y la piola conectada al acelerador del motor. La pieza corresponde a una platina de acero móvil a través de unos ejes (Figura 7), en donde por un extremo se conecta la piola del acelerador, y por el otro se encajan las piolas de los sistemas manual y eléctrico. El actuador eléctrico corresponde a un servomotor Dynamixel ex-106+ [4].

EL5004 - Taller de Diseño


Figura 7: CAD de platina con los ejes como guía.

Las tres secciones de piola conectadas a la platina deben estar tensadas en el reposo, lo que causa el movimiento de la platina si se presiona el pedal del acelerador (sistema manual) o si se rota el disco de giro servomotor (sistema eléctrico) y por ende, se accionará el acelerador del motor del goKart (Figura 8). Esta propuesta parte de la premisa que las piolas pueden aflojarse cierta cantidad, pues al momento de activar un sistema de acelerador, la piola del otro quedará en desuso. Cabe destacar que el desplazamiento máximo de la piola para acelerar, en el sistema manual original, es de aproximadamente 3 cm.


Figura 8: Diseño CAD del actuador del acelerador.

Como medida de seguridad se optó por ubicar un resorte en el extremo de la platina cercano al motor, de manera que el sistema tienda a detener la aceleración con la fuerza del resorte y no del sistema intrínseco del motor del goKart.

### 2.3.3. Resultados

La idea de deslizar una pieza por una guía se mantuvo, con la diferencia del tipo de piezas a utilizar. Finalmente se implementó un sistema con una corredera telescópica con rodamientos. Esto fue por el ínfimo roce que se opone al movimiento en comparación a una platina de acero.

EL5004 - Taller de Diseño

Por otro lado, para generar holguras en las piolas y evitar fuerzas no deseadas por la piola en desuso cuando se active uno de los dos sistemas de aceleración, se optó por conectar las piolas a la corredera por medio de topes móviles (Figura 9). La configuración en reposo consiste en tener las tres piolas tensas, y al momento de accionar un actuador la piola correspondiente jalará la corredera, mientras la otra estará en reposo, desacoplándose a la corredera.
En la Figura 9a se muestra el estado en reposo, en donde las tres piolas se encuentran en una tensión que ocasiona que la corredera esté cercana al motor del goKart. La Figura 9b indica una aceleración efectuada por el servomotor, de manera que la corredera se aleja del motor del goKart y la piola de sistema manual queda en un reposo parcial. Por último, en la Figura 9c se tiene una aceleración manual, por lo que se obseva la corredera alejada del motor del vehículo, mientras que la piola del servomotor está en desuso.


(a) Sistema en reposo. | (b) Sistema accionado por motor.


(c) Sistema accionado manualmente.

Figura 9: Actuador del acelerador en sus estados principales.

Por otro lado, en las imágenes de la Figura 9 se puede observar un resorte en el extremo de la corredera cercano al motor del goKart. Es el resorte de seguridad que se encarga de devolver la corredera al estado de reposo mientras ninguno de los sistemas de aceleración se activen.

## 3. Diseño eléctrico

En esta sección se muestran los distintos elementos del desarrollo en el plano eléctrico y electrónico.

### 3.1. Diagrama eléctrico

La Figura 10 muestra el diagrama eléctrico principal, este cuenta con los siguientes elementos:

EL5004 - Taller de Diseño

Batería: La batería corresponde a un pack de 4 celdas de polímero de litio. Posee un voltaje nominal de 14.8 V y una capacidad de 3300 mA h. Este tipo de baterías se caracterizan por su gran densidad energética y capacidad de descarga, por lo es óptima para la operación de motores, pues usualmente requieren peaks corriente del orden de 5 A.

Panel de control: En su interior contiene el microcontrolador y receptor de radio.

Interruptor principal: Es el encargado de conectar la batería con el resto de los circuitos.

Interruptor de emergencia: Desconecta la energía del bus de actuadores Dynamixel, no interfiere con la alimentación del panel de control.

Bus Dynamixel: Este bus esta constituido por cuatro conductores. Dos de ellos proporcionan alimentación a los dispositivos conectados (Vcc y tierra). Los otros dos corresponden a la señal diferencial del bus RS485.

Figura 10: Diagrama elétrico principal.

### 3.2. Sistema de radio

Para la comunicación con el GoKart a través de telecomandos se está utilizando un transmisor de radiofrecuencias llamado Fly-Sky modelo FS-T6, junto a un receptor de 6 canales a 2.4 GHz llamado Fly-Sky modelo FS-R6B (ver en Figura 11).


(a) Control remoto | (b) Receptor de radio

Figura 11: Hardware utilizado para telecomandar el gokart

EL5004 - Taller de Diseño

De la radio transmisora se utilizarán 3 comandos:

1. Manilla izquierda: movimientos UP y DOWN para acelerar y frenar, respectivamente.
2. Manilla derecha: movimientos LEFT y RIGHT para dirección.
3. Switch superior izquierda: para activar estado de emergencia.

De esta forma, el receptor utiliza 3 de sus 6 canales para recibir los datos, los que resultan ser números enteros con un rango entre 1000-1400, que corresponden al valor en µs del up-time de la señal PWM recibida.

### 3.3. Sistema embebido

El sistema cuenta con un microcontrolador principal encargado de recibir los comandos desde el receptor de radio y enviar comandos de movimiento a los servomotores. El sistema usa como elemento principal una placa de desarrollo Arduino Mega 2560 [1], que se muestra en la Figura 12. La Tabla 3 muestra las principales características de la placa de desarrollo.

Microcontrolador | ATmega2560
Voltaje de operación | 5 V
Limites de alimentación | 6 V a 20 V
GPIO | 54
Entradas ADC | 16
Memoria Flash | 256 kB
SRAM | 8 kB
Velocidad de reloj | 16 MHz
Puertos UART | 4

Tabla 3: Características Arduino Mega 2560


Figura 12: Arduino Mega 2560.

EL5004 - Taller de Diseño

### 3.3.1. Pantalla LCD

La pantalla LCD empleada corresponde a LCD keypad shield [2], esta placa es compatible con el extendido controlador Hitachi HD44780. La Figura 13 muestra la placa utilizada.


Figura 13: LCD keypad shield utilizado.

### 3.3.2. Interfaz con motores Dynamixel

Los actuadores utilizados en este proyecto corresponden al modelo Dynamixel EX-106+ fabricados por Robotis. Estos actuadores son ampliamente utilizados en aplicaciones robóticas, integran su propio controlador, encoder, driver e interfaz de comunicación que permite la conexión de múltiples actuadores usando como capa física un bus RS485.
Para la conversión del puerto UART del del microcontrolador al estándar RS485 es necesario un transceiver, en está aplicación se uso un integrado SN75176BP de Texas Instruments [3].
Para la comunicación con los actuadores Dynamixel es necesario usar un protocolo especificado por el fabricante [4], dado la gran extensión de estos motores existen librerías que proveen una interfaz de software que implementan el protocolo.

### 3.3.3. PCB

Para el montaje del receptor de radio y componentes necesarios para la comunicación con los motores Dynamixel, se diseñó y construyó una PCB que se se empotra de forma natural a la placa Arduino Mega, pues se ha usado el formato conocido como shield.
La Figura 14 muestra el diseño de la PCB, donde se ha considerado las conexiones para el transceiver RS485, una pantalla LCD y potenciómetros para hacer una interfaz de usuario.

EL5004 - Taller de Diseño


Figura 14: PCB con formato shield.

## 4. Software

El software que ejecuta el microcontrolador para comunicar la radio transmisora y los actuadores en el auto se realizó utilizando un modelo de comunicación robusto, que garantizara el correcto funcionamiento del auto, activara rápidamente los casos de emergencia y ofreciera fácilmente una forma de comunicar la información al usuario del auto a través de una pantalla LCD (ver Sección 3.3).
Dado que el el toolchain AVR GCC, usado para compilar el código para el microcontrolador, soporta el lenguaje C++, se hace en uso extensivo de programación orientada a objetos. Los elementos principales dentro del software (clases dentro del código) se detallan a continuación:

GoKartHW: Es el objeto principal o cerebro del código, al inicializarlo se inician los objetos que caracterizan los actuadores, la comunicación con el transmisor y con el LCD. También maneja el estado de emergencia, que implica detener frenar el auto y dejarlo con dirección hacia el centro.

Dxl servo: Es el objeto encargado de la comunicación con los motores Dynamixel y configura los parámetros de velocidad, torque y posiciones mínimas y máximas que tienen actuadores. Estos objetos heredan de esta clase:

1. Throttle: Es el objeto que representa al actuador del acelerador y configura sus parámetros acorde a las características físicas de ese actuador en el montaje.
2. Brake: Es el objeto que representa al actuador del freno y configura sus parámetros acorde a las características físicas de ese actuador en el montaje.
3. Steering Wheel: Es el objeto que representa al actuador ligado al manubrio y configura sus parámetros acorde a las características físicas de ese actuador en el montaje.

RFInterface: Es el objeto que controla el proceso de lectura de datos del receptor desde el transmisor RF. Este objeto recibe estos datos, los valida (según una configuración propia) y mapea hacia los actuadores. En caso de que los datos estén corruptos o no se estén recibiendo, entonces comanda al Gokart al estado de emergencia.

LCD: Es el objeto que controla la pantalla LCD, su escritura y la forma en que se muestren y limpien los datos en la pantalla. Por tanto, a través de este objeto el Gokart envía los mensajes de los procesos que desee mostrar.

EL5004 - Taller de Diseño

Se ha hecho uso de herramientas de control de versiones e integración continua para el desarrollo de software de forma colaborativa. Esto permite que, de forma automatizada, cada aporte sea validado antes de su integración en el desarrollo principal.

## Referencias

[1] Arduino. | Arduino | Mega | board | description. | https://www.arduino.cc/en/Main/
ArduinoBoardMega2560. (https://www.arduino.cc/en/Main/ArduinoBoardMega2560)
[2] DFRobot. LCD keypad shield description. http://www.dfrobot.com/wiki/index.php/LCD_KeyPad_Shield_For_Arduino_SKU:_DFR0009. (http://www.dfrobot.com/wiki/index.php/LCD_KeyPad_Shield_For_Arduino_SKU:_DFR0009)
[3] Texas Instruments Inc. SNx5176B Differential Bus Transceivers. http://www.ti.com/lit/ds/symlink/sn75176b.pdf. (http://www.ti.com/lit/ds/symlink/sn75176b.pdf)
[4] Ltd. Robotis Co. | Dynamixel EX-106 User Manual. | http://www.hizook.com/files/users/3/
EX-106_Robotis_Dynamixel_Servo_UserGuide.pdf. (http://www.hizook.com/files/users/3/EX-106_Robotis_Dynamixel_Servo_UserGuide.pdf)

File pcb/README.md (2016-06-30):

# EL5004: Teleoperación de Go Kart

## PCB

El software empleado corresponde [Eagle](http://www.cadsoftusa.com/download-eagle/) (versión >= 7.4).

## Dependencias

* [SparkFun Eagle Libraries](https://github.com/sparkfun/SparkFun-Eagle-Libraries)
* [Librería Eagle Lab. Mecatrónica](https://github.com/mecatronica-fcfm/mecatronica_eagle_lib)

## Componentes principales

* [RS485 Transceiver TI SN75176BP](http://www.ti.com/lit/gpn/sn75176b)

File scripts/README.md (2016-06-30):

# EL5004: Teleoperación de Go Kart

## Scripts de compilación y CI

Para compilar ejemplos se debe ejecutar:

```
$ cd el5004
$ ./scripts/build.sh .
```

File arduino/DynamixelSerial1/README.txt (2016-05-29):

**********************************   README FILE   ***************************************

Contact: Savage Electronics - Electronics For Everyone
  Autor:  Josue Alejandro Savage
  E-mail: savageelectronics@gmail.com 
  Web:    http://savageelectrtonics.blogspot.com/ 

Version: Dynamixel Library 15/01/2012 GPL v2.1

 Dynamixel Serial1 Version 1.2.0

Requeriments:

Arduino IDE Version 1.0
Wiring IDE 0100

Installation:

Copy the files to your IDE libraries folder.

examples:

In the Program:
Copy "DynamixelSerial" folder to Arduino/Contents/Resources/Java/libraries. 

or

In the SketchBook:
Copy "DynamixelSerial" folder to Arduino/libraries.

License:

 Dynamixel Half Duplex USART Comunication
 Copyright (c) 2011 Savage Electronics.
 Created by Savage on 27/01/11.
 
 This library is free software; you can redistribute it and/or
 modify it under the terms of the GNU Lesser General Public
 License as published by the Free Software Foundation; either
 version 2.1 of the License, or (at your option) any later version.
 
 This library is distributed in the hope that it will be useful,  
 but WITHOUT ANY WARRANTY; without even the implied warranty of
 MERCHANTABILITY or FITNESS FOR A PARTICULAR PURPOSE.  See the GNU
 Lesser General Public License for more details.
 
 You should have received a copy of the GNU Lesser General Public
 License along with this library; if not, write to the Free Software
 Foundation, Inc., 51 Franklin St, Fifth Floor, Boston, MA  02110-1301  USA

ChangeLog:

 25/07/2011 - Eliminado la modificacion serial para ser modificada dentro del mismo Hardware Serial.
 25/07/2011 - Modificado la funcion setBD() para aceptar todas la velocidades sin PDF.
 25/07/2011 - Agregada la funcion de Rotacion Continua.
 26/07/2011 - Agregada la funcion begin sin seteo de Direction_Pin.
 25/07/2011 - Agregada la funcion Reset.
 26/07/2011 - Agregada la funcion Reg_Write en move y moveSpeed.
 26/07/2011 - Agregada la funcion Action.
 13/12/2011 - Arreglado el manejo y envio de variables.
 22/12/2011 - Compatible con la actualizacion Arduino 1.0.
 10/01/2012 - Utilizacion de Macros y eliminacion codigo no necesario.
 11/01/2012 - Agregadas las funciones:
              int setTempLimit(unsigned char ID, unsigned char Temperature);
              int setAngleLimit(unsigned char ID, int CWLimit, int CCWLimit);
              int setVoltageLimit(unsigned char ID, unsigned char DVoltage, unsigned char UVoltage);
              int setMaxTorque(unsigned char ID, int MaxTorque);
              int setSRL(unsigned char ID, unsigned char SRL);
              int setRDT(unsigned char ID, unsigned char RDT);
              int setLEDAlarm(unsigned char ID, unsigned char LEDAlarm);
              int setShutdownAlarm(unsigned char ID, unsigned char SALARM);
              int setCMargin(unsigned char ID, unsigned char CWCMargin, unsigned char CCWCMargin);
              int setCSlope(unsigned char ID, unsigned char CWCSlope, unsigned char CCWCSlope);
15/01/2012 - Agregadas las funciones:
              int setPunch(unsigned char ID, int Punch);
              int moving(unsigned char ID);
              int lockRegister(unsigned char ID);
              int RWStatus(unsigned char ID);
              int readSpeed(unsigned char ID);
              int readLoad(unsigned char ID);

 TODO:
 
 FUNCION SYNCWRITE.

******************************************************************************************

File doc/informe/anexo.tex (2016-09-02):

\section{Anexo}
\subsection{Dirección}
Se incluye los planos de las piezas realizadas

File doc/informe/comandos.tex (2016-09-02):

% Figura
\begin{figure}[H]
\begin{center}
	
	\caption{Mensaje para modular usando FM.}
	\label{msg}
\end{center}
\end{figure}

% Subfigura 1x2
\begin{figure}[H]
    \centering
    \begin{subfigure}[b]{0.45\textwidth}
            
            \caption{Señal original.}
    \end{subfigure}%
    ~ 
    \begin{subfigure}[b]{0.45\textwidth}
            
            \caption{Señal filtrada.}
    \end{subfigure}
    \caption{Efectos de los filtros implementados.}
\end{figure}

% Subfigura 1x3
\begin{figure}[H]
    \centering
    \begin{subfigure}[b]{0.3\textwidth}
            
            \caption{4 \textit{clusters}.}
    \end{subfigure}%
    ~ 
    \begin{subfigure}[b]{0.3\textwidth}
            
            \caption{5 \textit{clusters}.}
    \end{subfigure}
    ~ 
    \begin{subfigure}[b]{0.3\textwidth}
            
            \caption{6 \textit{clusters}.}
    \end{subfigure}
    \caption{Gráficos de silueta para distintos números de \textit{clusters}.}\label{fig-multi-sil}
\end{figure}

% Arreglo de ecuaciones
\begin{eqnarray}
T &=& 1.5(t_2 - t_1) \\
L  &=& 1.5(t_1 - \frac{1}{3}t2)
\end{eqnarray}

% Lista
\begin{itemize}
\item Filtros
\item Normalización
\end{itemize}

% Poner codigo fuente, guardar en carpeta src
\lstinputlisting[label=matlab-coef,caption=Códigos de calculo de parámetros.]{src/coef.m}

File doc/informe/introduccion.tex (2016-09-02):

\section{Introducción}

Este trabajo se enmarca dentro del contexto del curso EL5004 Taller de Diseño, en el que se lleva a cabo un proyecto multidisciplinario entre estudiantes de ingeniería mecánica e ingeniería eléctrica, con el fin de lograr el acercamiento entre ambas disciplinas y el aprendizaje que esto conlleva, no solo de trabajo en equipo sino de acercar a los estudiantes a lo que corresponde a un proyecto real junto a todas sus partes: concebir, diseñar, implementar y operar.
En este caso, se propone desarrollar una teleoperación de un vehículo tipo goKart construido por alumnos del departamento de ingeniería mecánica. Esto es, comandar a distancia las acciones de giro, aceleración y freno de este vehículo. Para ello se debe realizar un diseño mecánico para el montaje de los nuevos mecanismos, como así un diseño eléctrico de la conexión y comunicación entre los actuadores.

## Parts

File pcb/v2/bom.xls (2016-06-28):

Bill of materials
Concepto | Código | Cantidad | Precio unitario | Precio | Lugar de compra
RS485 Transceiver | SN75176BP | 1 |  |  | Victronics

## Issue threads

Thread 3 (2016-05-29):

Mejor manejo de clases para comunicación

rorromr, 2016-05-29:
RFInterface es una clase para el manejo de la comunicación con el módulo RF, se propone crear una estructura de clases para que se puedan implementar otros tipos de comunicación (eg Serial) que posean la misma interfaz.

dawei22, 2016-05-29:
Obetos

rorromr, 2016-05-30:
Si, debería haber una especie de ComManager, que el manejara las distintos tipos de comunicación y ofreciera una interfaz común independiente de lo que pasa por atras. Este obeto sería miembro del obeto GoKart, así lo veo yo

rorromr, 2016-06-03:
RFInterface ya implementa ComInterface, solo falta el manager. Trabajar en rama fix-rf-interface.

dawei22, 2016-06-12:
Ready

Closed 2016-06-24.

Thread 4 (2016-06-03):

Pruebas sobre rama fix-rf-interface

rorromr, 2016-06-03:
La rama ya contiene rf_interface implementando getCommand de forma heredada. Por favor trabajar en esa rama.
TODO:
- [ ] Pruebas con hardware
- [ ] Map de valores para la construcción de GoKartCommand
- [ ] Configurar estado de emergencia

Closed 2016-07-09.

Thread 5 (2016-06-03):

Mejoras en librería Dynamixel

rorromr, 2016-06-03:
TODO:
- [ ] Pruebas de rendimiento bajo carga
- [ ] Reducir tiempos de return delay
- [x] Mejorar estructura de buffer o reeimplementar usando interrupciones
- [ ] Configurar estado de emergencia

Closed 2016-09-02.

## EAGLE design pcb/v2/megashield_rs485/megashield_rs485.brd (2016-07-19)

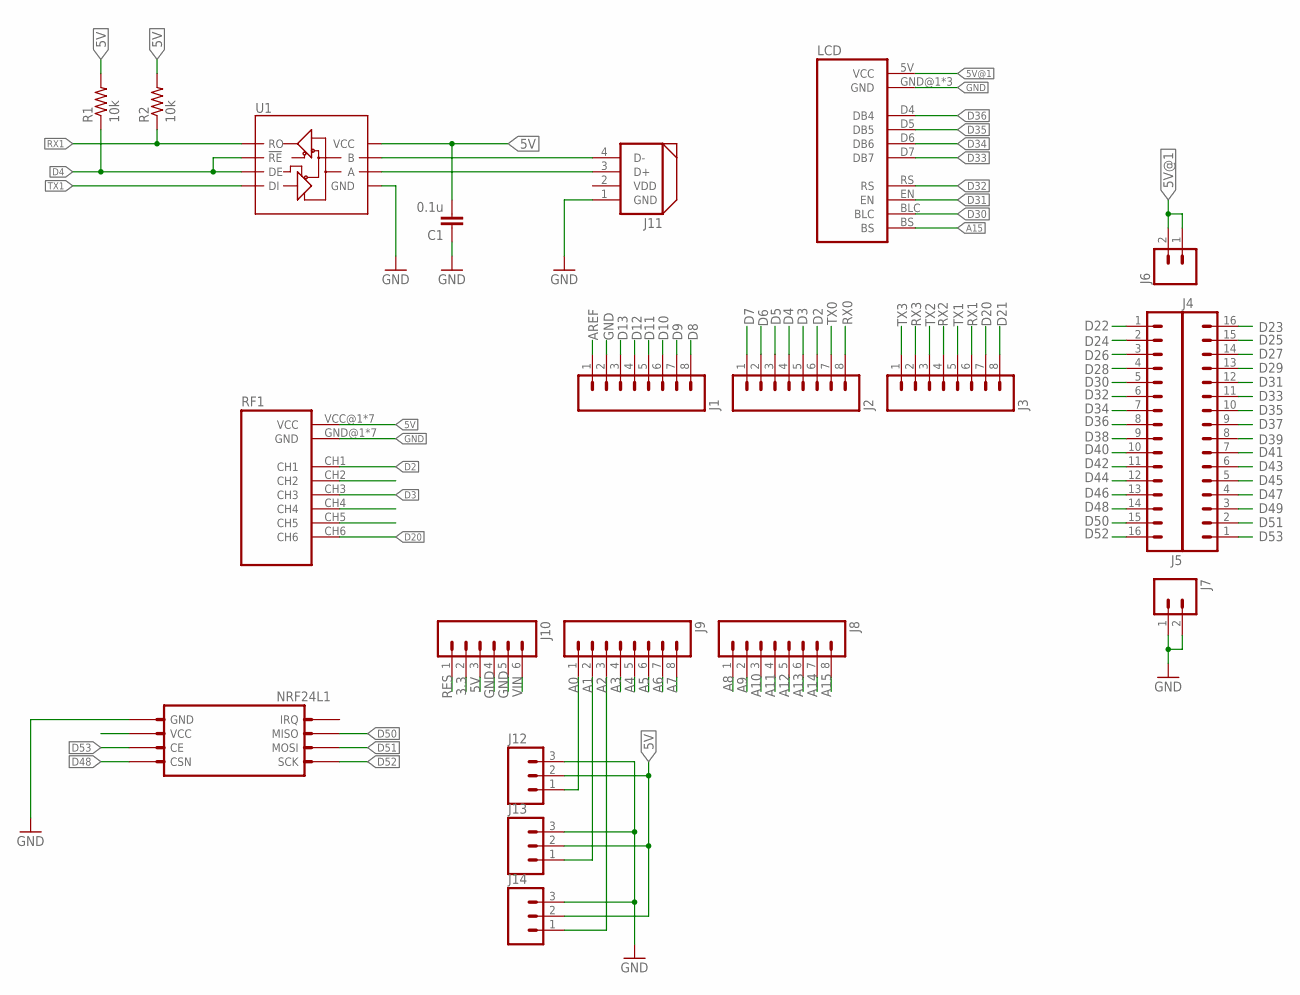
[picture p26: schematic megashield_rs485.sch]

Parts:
C1: 0.1u; CAP-PTH-SMALL
J1, J2, J3, J8, J9: M08LONGPADS; 1X08_LONGPADS
J4, J5: M16PTH; 1X16
J6, J7: M02PTH; 1X02
J10: M06LONGPADS; 1X06_LONGPADS
J11: DYNAMIXEL_RS485; DYNAMIXEL_SPOX_04
J12, J13, J14: M03PTH; 1X03
LCD: LCD_SHIELD
NRF24L1: NRF
R1, R2: 10k; AXIAL-0.4
RF1: FS_R6B
U1: RS485; DIL08

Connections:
3.3: J10.2
5V: C1.2, J10.3, J12.2, J13.2, J14.2, R1.P$2 (2), R2.P$2 (2), RF1.VCC@1 (VCC), RF1.VCC@2 (VCC), RF1.VCC@3 (VCC), RF1.VCC@4 (VCC), RF1.VCC@5 (VCC), RF1.VCC@6 (VCC), RF1.VCC@7 (VCC), U1.8 (VCC)
5V@1: J6.1, J6.2, LCD.5V (VCC)
A0: J9.1, J12.1
A1: J9.2, J13.1
A2: J9.3, J14.1
A3: J9.4
A4: J9.5
A5: J9.6
A6: J9.7
A7: J9.8
A8: J8.1
A9: J8.2
A10: J8.3
A11: J8.4
A12: J8.5
A13: J8.6
A14: J8.7
A15: J8.8, LCD.BS
AREF: J1.1
D2: J2.6, RF1.CH1
D3: J2.5, RF1.CH3
D4: J2.4, R1.P$1 (1), U1.2 (!RE), U1.3 (DE)
D5: J2.3
D6: J2.2
D7: J2.1
D8: J1.8
D9: J1.7
D10: J1.6
D11: J1.5
D12: J1.4
D13: J1.3
D20: J3.7, RF1.CH6
D21: J3.8
D22: J5.1
D23: J4.16
D24: J5.2
D25: J4.15
D26: J5.3
D27: J4.14
D28: J5.4
D29: J4.13
D30: J5.5, LCD.BLC
D31: J4.12, LCD.EN
D32: J5.6, LCD.RS
D33: J4.11, LCD.D7 (DB7)
D34: J5.7, LCD.D6 (DB6)
D35: J4.10, LCD.D5 (DB5)
D36: J5.8, LCD.D4 (DB4)
D37: J4.9
D38: J5.9
D39: J4.8
D40: J5.10
D41: J4.7
D42: J5.11
D43: J4.6
D44: J5.12
D45: J4.5
D46: J5.13
D47: J4.4
D48: J5.14, NRF24L1.4 (CSN)
D49: J4.3
D50: J5.15, NRF24L1.7 (MISO)
D51: J4.2, NRF24L1.6 (MOSI)
D52: J5.16, NRF24L1.5 (SCK)
D53: J4.1, NRF24L1.3 (CE)
GND: C1.1, J1.2, J7.1, J7.2, J10.4, J10.5, J11.1 (GND), J12.3, J13.3, J14.3, LCD.GND@1 (GND), LCD.GND@2 (GND), LCD.GND@3 (GND), NRF24L1.P$1 (GND), RF1.GND@1 (GND), RF1.GND@2 (GND), RF1.GND@3 (GND), RF1.GND@4 (GND), RF1.GND@5 (GND), RF1.GND@6 (GND), RF1.GND@7 (GND), U1.5 (GND)
unnamed: J11.3 (D+), U1.6 (A)
unnamed: J11.4 (D-), U1.7 (B)
RES: J10.1
RX0: J2.8
RX1: J3.6, R2.P$1 (1), U1.1 (RO)
RX2: J3.4
RX3: J3.2
TX0: J2.7
TX1: J3.5, U1.4 (DI)
TX2: J3.3
TX3: J3.1
VDD: J11.2 (VDD)
VIN: J10.6

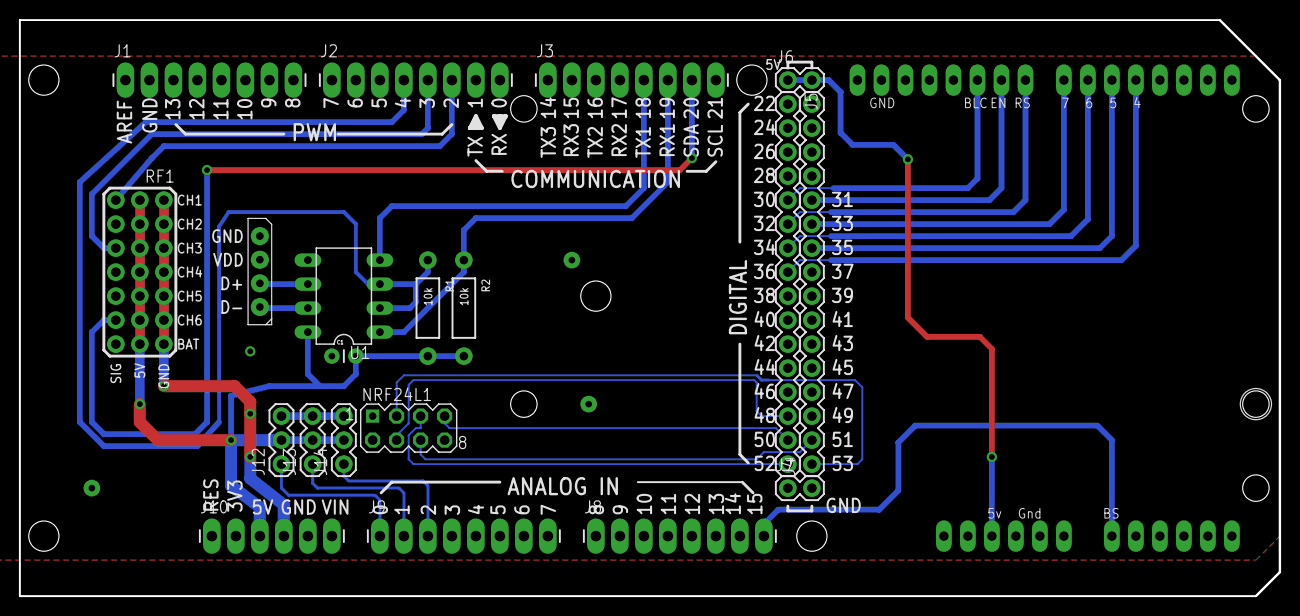
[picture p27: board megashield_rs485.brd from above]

Board: 2 copper layers, 133.4 x 61.0 mm, 21 parts (0 on the bottom side), 27 nets.

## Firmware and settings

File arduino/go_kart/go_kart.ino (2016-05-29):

#include "Arduino.h"
#include "DynamixelSerial1.h"
#include "rf_interface.h"
#include "dxl_servo.h" 

// Dynamixel protocol
#define GOKART_DXL_BAUDRATE 200000
#define GOKART_DXL_CTRL_PIN 2

GoKart::RFInterface rf(3);

GoKart::DxlServo brake(Dynamixel, 5);

void setup()
{
  Dynamixel.begin(GOKART_DXL_BAUDRATE,GOKART_DXL_CTRL_PIN);
  brake.config(100, 200, 50);
  
  rf.addChannel(1,6); // Channel 1 connected on 6 pin
  rf.addChannel(2,7); // Channel 2 connected on 7 pin
  rf.addChannel(3,8); // Channel 3 connected on 8 pin
}

void loop()
{
  rf.update();
  // Print values
  Serial.print("Ch1: "); Serial.println(rf.getChannel(1));
  Serial.print("Ch2: "); Serial.println(rf.getChannel(2));
  Serial.print("Ch3: "); Serial.println(rf.getChannel(3));
}

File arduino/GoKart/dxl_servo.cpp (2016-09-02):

#include "dxl_servo.h"

namespace GoKart
{
  
  DxlServo::DxlServo(DynamixelClass& dxl, const uint8_t id):
    dxl_(&dxl),
    id_(id)
  {
    if (!dxl_)
    {
      ERROR_PRINT_NAMED("DxlServo/config", "Null interface "); ERROR_PRINTLN_RAW(id_);
      set_error(&status_, DXL_SERVO_NULL_INTERFACE);
    }
  }

  bool DxlServo::init(const uint16_t min, const uint16_t max, const uint16_t zero)
  {
    min_ = min;
    max_ = max;
    zero_ = zero;

    if (!dxl_)
    {
      ERROR_PRINT_NAMED("DxlServo/config", "Null interface "); ERROR_PRINTLN_RAW(id_);
      set_error(&status_, DXL_SERVO_NULL_INTERFACE);
      return false;
    }

    // Set config
    uint8_t error = 0U;
    error = dxl_->setCWLimit(id_, min_);
    error = dxl_->setCCWLimit(id_, max_);
    if (error)
    {
      ERROR_PRINT_NAMED("DxlServo/config", "Servo fail config "); ERROR_PRINTLN_RAW(id_);
      set_error(&status_, DXL_SERVO_ERROR_CONFIG);
      return false;
    }

    set_error(&status_, DXL_SERVO_OK);
    return true;
  }

  void DxlServo::move(const int16_t pos_target, const int16_t vel_target)
  {
    dxl_->moveSpeed( id_, pos_target, vel_target);
  }

  int16_t DxlServo::getPosition()
  {
    return dxl_->readPosition(id_);
  }

  void DxlServo::moveToZero()
  {
    dxl_->move(id_,zero_);
  }
  
  int16_t DxlServo::getCCWLimit()
  {
    return dxl_->readCCWLimit(id_);
  }

  int16_t DxlServo::getCWLimit()
  {
    return dxl_->readCCWLimit(id_);
  }

  int16_t DxlServo::setCCWLimit(uint16_t limit)
  {
    return dxl_->setCCWLimit(id_, limit);
  }

  int16_t DxlServo::setCWLimit(uint16_t limit)
  {
    return dxl_->setCWLimit(id_, limit);
  }

  int16_t DxlServo::torqueEnable(bool torque_enable)
  {
    return dxl_->torqueStatus(id_, torque_enable);
  }

  int16_t DxlServo::getLoad()
  {
    return dxl_->readLoad(id_);
  }


  bool DxlServo::check()
  {
    DEBUG_PRINTLN_NAMED("dxl_servo/check","check");
    // Ping check
    uint8_t ping_attempts = 0U;
    uint8_t ping_status = 0U;
    while(!ping_status && ping_attempts < DXL_SERVO_PING_ATTEMPTS)
    {
      DEBUG_PRINT_NAMED("dxl_servo/check","ping attempt with servo "); DEBUG_PRINTLN_RAW(id_);
      ping_status = dxl_->ping(id_) == -1 ? 0U : 1U;
      ++ping_attempts;
    }
    if (!ping_status)
    {
      ERROR_PRINT_NAMED("dxl_servo/check", "Servo not found "); ERROR_PRINTLN_RAW(id_);
      set_error(&status_, DXL_SERVO_NOT_FOUND);
      return false;
    }
    // Check angles
    uint16_t pos = dxl_->readPosition(id_);
    if (pos > max_)
    {
      ERROR_PRINT_NAMED("dxl_servo/check","Servo max angle CCW "); ERROR_PRINTLN_RAW(id_);
      set_error(&status_, DXL_SERVO_MAX_ANGLE_CW);
      return false;
    }
    else if (pos < min_)
    {
      ERROR_PRINT_NAMED("dxl_servo/check","Servo max angle CW "); ERROR_PRINTLN_RAW(id_);
      set_error(&status_, DXL_SERVO_MAX_ANGLE_CCW);
      return false;
    }

    set_error(&status_, DXL_SERVO_OK);
    return true;
  }
  
}

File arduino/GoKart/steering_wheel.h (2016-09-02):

/**
 * @brief Steering Wheel
 * @author Rodrigo Muñoz
 * @date 2016
 *
 * @TODO
 *
 */

#ifndef GOKART_STEERINGWHEEL_H
#define GOKART_STEERINGWHEEL_H

#include "dxl_servo.h"

#define GOKART_SW_CW_ENCODER (900)
#define GOKART_SW_CCW_ENCODER (3200)
#define GOKART_SW_CENTER_ENCODER (2048)
#define GOKART_SW_DEFAULT_SPEED (300)
#define GOKART_SW_COMMAND_FACTOR (1.0f/128.0f)
#define GOKART_SW_POS_MAP_FACTOR ((GOKART_SW_CENTER_ENCODER-GOKART_SW_CW_ENCODER)*GOKART_SW_COMMAND_FACTOR)
#define GOKART_SW_NEG_MAP_FACTOR ((GOKART_SW_CCW_ENCODER-GOKART_SW_CENTER_ENCODER)*GOKART_SW_COMMAND_FACTOR)

namespace GoKart
{
  class SteeringWheel: public DxlServo
  {
    public:
      SteeringWheel(DynamixelClass& dxl, const uint8_t id);

      bool init();
      
      void move(const int8_t pos_target);

      void center();

      void setSpeed(const uint16_t speed);

    private:
      uint16_t speed_;

  };
}

#endif

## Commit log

2016-05-25 Estructura de archivos
2016-05-25 Archivo BOM, PCB base para shield
    [bom.xls, megashield_rs485.brd, megashield_rs485.sch]
2016-05-29 Interfaz para servos
2016-05-29 Metodos para freno
2016-05-29 Interfaz para actuadores y clase para abstracción del GoKart
2016-05-29 Software como librería de Arduino
2016-05-31 Manejo de codigos de error en Servo
    [dxl_servo.cpp]
2016-06-02 Implementacion de RF funcionando, falta completar match para getCommand
2016-06-02 Modificacion de libreria para reemplazar a digitalWrite
2016-06-02 Clase RF Interface implementa metodos de ComInterface
2016-06-02 Fix SetTx and SetRx functions using inline
    [DynamixelSerial1.cpp, DynamixelSerial1.h]
2016-06-03 March entre valroes RF y enteros para motores en Rf_getCommand
2016-06-06 manejo de clases
2016-06-08 Añadir funciones de debug y configuración de limites
2016-06-08 Fix funciones para set de angulos
    [DynamixelSerial1.cpp, DynamixelSerial1.h, dynamixel_test.ino]
2016-06-09 Configuración de angulos máximos y minimos OK
2016-06-09 Fix mensajes de debug y metodos de servomotor
    [dxl_servo.cpp, dynamixel_test.ino, gokart_dynamixel.ino]
2016-06-09 Mejoras en manejo de errores y configuracion de angulos limites
    [dxl_servo.cpp]
2016-06-15 Prueba de test gokar_integration y probado en el dxl real.
2016-06-16 Mapeo de comando para steering wheel y comandos de velocidad
2016-06-23 Fix max value for steering wheel command mapping
    [rf_interface.cpp, rf_test2.ino]
2016-06-24 Test velocity command in steering wheel
2016-06-24 Emergency state and fix center in steering wheel
    [brake.cpp, brake.h, gokart.cpp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]
2016-06-24 Mejoras en metodos de GoKart, map para freno y metodos init para servos
2016-06-24 Fix println on gokart init method
    [gokart.cpp]
2016-06-24 Map de acelerador
2016-06-24 Mejoras en scripts de CI
2016-06-28 PCB template
    [megashield_rs485.brd, megashield_rs485.sch]
2016-06-28 hecho el filtro del rf, falta probar si compila, probar en los pcs de la U
2016-06-28 Add rs485 transceiver
    [bom.xls, megashield_rs485.brd, megashield_rs485.sch]
2016-06-28 Add analog inputs
    [megashield_rs485.brd, megashield_rs485.sch]
2016-06-28 PCB con elementos para conexion de pantalla
    [megashield_rs485.brd, megashield_rs485.sch]
2016-06-30 fix rf_interface mean declaration
    [rf_interface.cpp, rf_interface.h]
2016-06-30 Modify pins for PCB
2016-07-02 Serialización de mensaje usando Python
2016-07-03 Basic example using serial interface
    [megashield_rs485.brd]
2016-07-07 Nueva lectura de pines RD con interruptores y tambien un enabled del uso del filtro. falta probar
2016-07-08 Print on LCD current command
2016-07-08 Motor config using LCD
2016-07-08 LCD test and brake motor limits
2016-07-09 Torque enable funcion
2016-07-09 Fix PCB dimension for better fit on Arduino board
    [megashield_rs485.brd]
2016-07-13 Add clear command, fix LCD test
    [gokart_lcd_test.ino, lcd.cpp, lcd.h]
2016-07-13 LCD test with print current command
2016-07-13 Implementacion de consistencia de datos y metodo init de RF
2016-07-13 Fix throttle
2016-07-15 Control de emergencia en apagado y estabilidad de valores
2016-07-15 Fix map for sw actuator
    [rf_interface.cpp]
2016-07-18 Fix servo selected in control panel
    [lcd.cpp, lcd.h]
2016-07-18 PCB with LCD
    [megashield_rs485.brd, megashield_rs485.sch]
2016-07-19 Add nRF24l01
    [megashield_rs485.brd, megashield_rs485.sch]
2016-07-20 PCB v2
    [bom.xls, megashield_rs485.brd, megashield_rs485.sch]
2016-07-20 Add PCB v1 and v2
    [bom.xls, megashield_rs485.brd, megashield_rs485.sch]
2016-07-20 sacar buffer, listo para mezclar con heuristica de pina
2016-07-20 mezcla de ramas mati con pina en master
2016-07-21 cambios en los limites del eoncder del motor direccion
2016-07-21 Function print2
2016-07-25 Diagram schematic
    [diagram.sch]
2016-09-11 CAD link

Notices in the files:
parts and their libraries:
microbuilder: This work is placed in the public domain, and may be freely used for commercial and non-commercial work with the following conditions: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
